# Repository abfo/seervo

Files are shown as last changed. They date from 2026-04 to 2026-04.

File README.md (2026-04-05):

# Seervo

An LLM powered ESP32 robot. This is an experiment in embodied AI, with a vision model connected to a camera and distance detector and deciding what to do next. For more information check out this [video](https://youtu.be/qIrNDQmVw1A) of the robot in action, and my [blog post](https://ithoughthecamewithyou.com/post/seervo-an-llm-powered-robot) about this project.

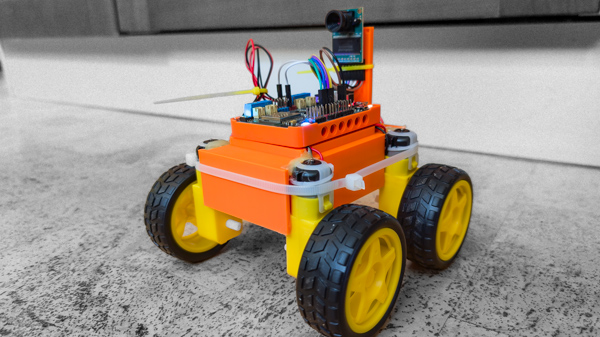
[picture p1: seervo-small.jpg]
Seervo


## Architecture 

For this project I wanted a server to make it easy to see what the robot is doing and to iterate on the prompts and control logic. The server folder has a very simple ASP.NET Core web API. The robot posts an image to the API and gets JSON with the next action to take. I run this in VS Code on Windows but it should run anywhere .NET 10 Core is supported. 

The client folder contains [MicroPython](https://micropython.org/) code to run the robot. There are simple drivers for the camera, motors, sonar, and LEDs and a control loop that calls the API and executes the JSON instructions. 

Lastly the chassis folder contains OpenSCAD and STL files to 3D print a basic chassis that holds the battery, controller, motors and camera. There is also a mounting bracket for a HC-SR04 ultrasonic range detector. 

## Getting Started

Follow the [notes](client/notes.md) in the client folder to flash MicroPython to the ESP32 and assemble the components. Use mpremote to copy python files to the board, and a .env file containing your WiFi SSID and password, i.e.:

```
mprempte cp camera.py :camera.py
```

3D print the chassis. This has alignment holes for the motors and I use a glue gun to hold these in place. I use a cable tie to attach the camera to the mast, and another to wrap around the chassis and secure the battery. 

Start the server up and switch on the robot! You'll need an OpenAI API key as an environment variable. 

## Tips and Ideas

My version is supposed to avoid pets and entertain humans. Edit Instructions.md to give the robot a different mission. 

The server currently uses GPT 5.4 with medium reasoning. I find this to be a good balance of speed and intelligence. It does chew up some money if you leave it running though. Drop down to a cheaper model and/or a lower camera resolution if you need this to be cheaper! 

It would be good to have an option for the robot to call ChatGPT directly, removing the server dependency. 

I'm also considering an image embedding model in parallel to the LLM call, so the robot can more easily detect if it's looking at the same scene and might be stuck.

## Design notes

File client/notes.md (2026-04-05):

# Seervo Client

## Getting Started

I'm using this [Maker-ESP32](https://github.com/nulllaborg/maker-esp32/tree/master?tab=readme-ov-file) board and working with micropython from VS Code. 

Create a virtual environment and install esptool and mpremote:

```python
pip install esptool mpremote
```

Grab the firmware ([this seems to work](https://micropython.org/resources/firmware/ESP32_GENERIC-20251209-v1.27.0.bin)) and install (board mounted as COM5 for me, there is a driver listed but hope not to have to install...):

```python
python -m esptool --port COM5 erase_flash
python -m esptool --port COM5 --baud 460800 write_flash 0x1000 ESP32_GENERIC-20251209-v1.27.0.bin
```

Run a quick test script to blink the LEDs:

```python
from machine import Pin
from neopixel import NeoPixel
import time

np = NeoPixel(Pin(16, Pin.OUT), 4)  # 4 onboard RGB LEDs on GPIO16

while True:
    for i in range(4):
        np[i] = (30, 0, 0)   # red
    np.write()
    time.sleep_ms(300)

    for i in range(4):
        np[i] = (0, 0, 0)    # off
    np.write()
    time.sleep_ms(300)
```

```python
mpremote run main.py
```

LEDs should now be blinking. 

## Camera

For this project I got the Arduino Mega256 SPI camera board (B0067). This wires into SPI/I2C and 3.3v power. There isn't a driver for the ESP32, camera.py handles photo capture. 

## Motors

The Maker-ESP32 has four motor drivers. I'm using [these](https://www.amazon.com/dp/B0D8H89XDY?ref_=ppx_hzsearch_conn_dt_b_fed_asin_title_1) generic motors and wheels. 

## Distance

A HC-SR04 ultrasonic range detector is wired to gnd / 5v / trigger (gpio 25) / echo (gpio 26). Echo need a voltage divider - echo pin to 1kΩ resistor and then from there one wire to gpio 26 and one to ground via a 2kΩ resistor.

```
Echo pin ──── 1kΩ ────┬──── GPIO 26
                       │
                      2kΩ
                       │
                      GND
```

## Power

I'm using [this](https://www.amazon.com/dp/B077Y9HNTF?th=1) battery and [these](https://www.amazon.com/dp/B0CPHJMW47) connectors for the charger and to plug into the Maker board. 

## Chassis 

See the Chassis folder for an OpenSCAD design and STL file.

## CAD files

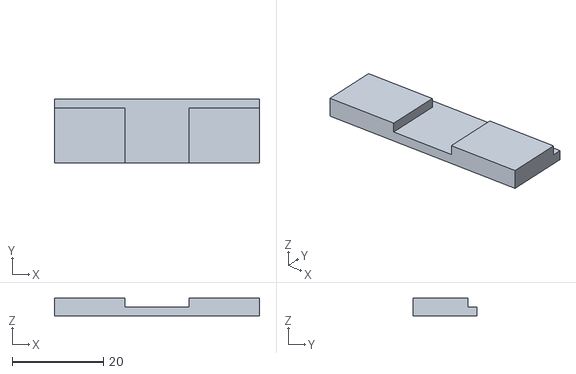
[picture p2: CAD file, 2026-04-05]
chassis/hc-sr04-plate.stl
45.0 x 14.0 x 3.95

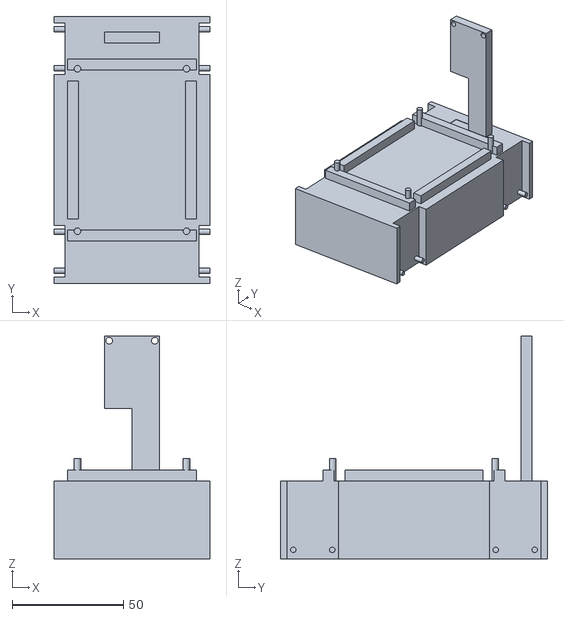
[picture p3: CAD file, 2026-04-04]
chassis/seervo.stl
70.0 x 120.0 x 100.0

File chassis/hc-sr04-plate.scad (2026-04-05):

// HC-SR04 mounting plate

base_w = 45;
base_d = 14;
base_h = 2;

side_w = 15.5;
side_d = 12;
side_h = 1.95;

union() {
    // Base plate
    cube([base_w, base_d, base_h], center = false);

    // Left raised section
    translate([0, 0, base_h])
        cube([side_w, side_d, side_h], center = false);

    // Right raised section
    translate([base_w - side_w, 0, base_h])
        cube([side_w, side_d, side_h], center = false);
}

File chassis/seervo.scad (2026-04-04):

// Outer box dimensions
outer_w = 70;
outer_l = 120;
outer_h = 35;

// Inner battery cavity
inner_w = 53;
inner_h = 32;
front_wall = 3;
back_overlap = 0.2;

// Motor cutouts
motor_cutout_l = 23;
motor_cutout_depth = 5;
corner_offset = 3;
side_overlap = 0.2;

// Motor mounting pegs
motor_peg_d = 2.5;
motor_peg_r = motor_peg_d / 2;
motor_peg_z = 4;         // center 4mm up from bottom
motor_peg_len = 5;       // protrudes 5mm into motor cutout
peg_offset_in_cutout = 2.75;

// Top circuit board mount
board_w = 58;
board_l = 82;
board_wall = 5;
board_wall_h = 5;
side_wire_gap = 10;

// Circuit board standoffs
standoff_inset = 4.5;
standoff_d = 3;
standoff_r = standoff_d / 2;
standoff_h = 10;

// Camera mast
mast_w = 24.5;
mast_l = 5;
mast_h = 65;

// Camera mast holes
mast_hole_d = 3;
mast_hole_r = mast_hole_d / 2;
mast_hole_side_inset = 2;
mast_hole_top_inset = 2;
mast_hole_overlap = 0.2;

// Camera mast cutout
mast_cutout_w = mast_w / 2;
mast_cutout_h = mast_h / 2;
mast_cutout_overlap = 0.2;

front_cutout_y = corner_offset;
rear_cutout_y  = outer_l - corner_offset - motor_cutout_l;

// Board footprint position
board_x0 = (outer_w - board_w) / 2;
board_y0 = (outer_l - board_l) / 2;

// Camera mast position
mast_x0 = (outer_w - mast_w) / 2;
mast_y0 = board_y0 + board_l + ((outer_l - (board_y0 + board_l)) - mast_l) / 2;

// Motor peg centers along the length dimension
motor_peg_y_positions = [
    front_cutout_y + peg_offset_in_cutout,
    front_cutout_y + motor_cutout_l - peg_offset_in_cutout,
    rear_cutout_y  + peg_offset_in_cutout,
    rear_cutout_y  + motor_cutout_l - peg_offset_in_cutout
];

// Mast hole positions
mast_hole_x_positions = [
    mast_x0 + mast_hole_side_inset,
    mast_x0 + mast_w - mast_hole_side_inset
];
mast_hole_z = outer_h + mast_h - mast_hole_top_inset;


// Main chassis body with all cutouts applied
module chassis_body() {
    difference() {
        union() {
            // Outer box
            cube([outer_w, outer_l, outer_h], center = false);

            // Top walls for circuit board mount
            translate([board_x0, board_y0, outer_h]) {
                // Front wall
                cube([board_w, board_wall, board_wall_h], center = false);

                // Back wall
                translate([0, board_l - board_wall, 0])
                    cube([board_w, board_wall, board_wall_h], center = false);

                // Left wall with front/back gaps
                translate([0, side_wire_gap, 0])
                    cube([
                        board_wall,
                        board_l - 2 * side_wire_gap,
                        board_wall_h
                    ], center = false);

                // Right wall with front/back gaps
                translate([board_w - board_wall, side_wire_gap, 0])
                    cube([
                        board_wall,
                        board_l - 2 * side_wire_gap,
                        board_wall_h
                    ], center = false);
            }

            // Circuit board standoffs
            for (x_pos = [board_x0 + standoff_inset, board_x0 + board_w - standoff_inset])
            for (y_pos = [board_y0 + standoff_inset, board_y0 + board_l - standoff_inset]) {
                translate([x_pos, y_pos, outer_h])
                    cylinder(h = standoff_h, r = standoff_r, $fn = 48);
            }

            // Camera mounting mast
            translate([mast_x0, mast_y0, outer_h])
                cube([mast_w, mast_l, mast_h], center = false);
        }

        // Inner battery cavity
        translate([
            (outer_w - inner_w) / 2,
            front_wall,
            (outer_h - inner_h) / 2
        ])
        cube([
            inner_w,
            outer_l - front_wall + back_overlap,
            inner_h
        ], center = false);

        // Motor cutouts: left side
        translate([
            -side_overlap,
            front_cutout_y,
            -side_overlap
        ])
        cube([
            motor_cutout_depth + side_overlap,
            motor_cutout_l,
            outer_h + 2 * side_overlap
        ], center = false);

        translate([
            -side_overlap,
            rear_cutout_y,
            -side_overlap
        ])
        cube([
            motor_cutout_depth + side_overlap,
            motor_cutout_l,
            outer_h + 2 * side_overlap
        ], center = false);

        // Motor cutouts: right side
        translate([
            outer_w - motor_cutout_depth,
            front_cutout_y,
            -side_overlap
        ])
        cube([
            motor_cutout_depth + side_overlap,
            motor_cutout_l,
            outer_h + 2 * side_overlap
        ], center = false);

        translate([
            outer_w - motor_cutout_depth,
            rear_cutout_y,
            -side_overlap
        ])
        cube([
            motor_cutout_depth + side_overlap,
            motor_cutout_l,
            outer_h + 2 * side_overlap
        ], center = false);

        // Camera mast holes
        for (x_pos = mast_hole_x_positions) {
            translate([x_pos, mast_y0 - mast_hole_overlap, mast_hole_z])
                rotate([-90, 0, 0])
                    cylinder(
                        h = mast_l + 2 * mast_hole_overlap,
                        r = mast_hole_r,
                        $fn = 48
                    );
        }

        // Camera mast cutout: lower-right quarter when viewed from behind
        translate([
            mast_x0 - mast_cutout_overlap,
            mast_y0 - mast_cutout_overlap,
            outer_h - mast_cutout_overlap
        ])
        cube([
            mast_cutout_w + mast_cutout_overlap,
            mast_l + 2 * mast_cutout_overlap,
            mast_cutout_h + mast_cutout_overlap
        ], center = false);
    }
}


// Motor pegs added AFTER cutouts so they remain visible
module motor_pegs() {
    // Left side pegs: extend from x=5 back out to x=0 into the cutout
    for (y_pos = motor_peg_y_positions) {
        translate([motor_cutout_depth, y_pos, motor_peg_z])
            rotate([0, -90, 0])
                cylinder(h = motor_peg_len, r = motor_peg_r, $fn = 48);
    }

    // Right side pegs: extend from x=65 out to x=70 into the cutout
    for (y_pos = motor_peg_y_positions) {
        translate([outer_w - motor_cutout_depth, y_pos, motor_peg_z])
            rotate([0, 90, 0])
                cylinder(h = motor_peg_len, r = motor_peg_r, $fn = 48);
    }
}


// Final model
union() {
    chassis_body();
    motor_pegs();
}

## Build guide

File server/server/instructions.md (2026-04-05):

# Robot Control

## Overview

You are a robot controller. You will be provided with a view from the robot's forward facing camera and a distance in meters to the closest object directly in front of the robot. You respond with motor and light controls in JSON format described below. Your objective is to explore your environment and visit four different rooms (a dining room, a kitchen, a hall and a living room). You should entertain any people you find with a small dance, and run away from any pets. It is more important to avoid pets than to entertain people. It's OK to visit rooms multiple times.

As your senses only face forwards you should move in that direction when possible and execute a tank turn to rotate in place when searching for a new direction to travel. Is is recommended that you operate your motors at speed 400 (so 400, 400 to move forwards, -400, 400 to turn, etc). Given this speed use the formula t = (1117.3 * d) + 72.2 to calculate how long to run the motors. In this formula t is time in milliseconds and d is distance in meters. For rotation use t = (2.8 * a) + 100. t is time in milliseconds again and a is angle in degrees. 15 degrees is a good amount to rotate when searching for a clear path forward. If you see a pet, rotate 180 degrees and then start searching for a safe escape path. 

Use your memories to store observations about controlling the robot and navigating your environment. If you see that you are behaving repetitively then try something new. You are brave and favor motion over caution. Try to keep moving as far as possible and explore as much as you can. Do not obsess over finding the right route. If you have space to move forwards, then move. Don't keep turning and rejecting what you see, when you can move, move. If you have less than 0.2 meters in front then rotate and search for a clear path. 

## Example JSON

You always respond with a JSON object following the pattern below. Do not escape the JSON, or include an explanation or other extra text. The JSON object is
being sent to the robot by a web service and will break if you don't follow the format carefully. Here is an example of a valid JSON response:

{
  "colors": [
    { "r": 30, "g": 10, "b": 5 },
    { "r": 25, "g": 10, "b": 0 },
    { "r": 15, "g": 15, "b": 30 },
    { "r": 30, "g": 0, "b": 15 }
  ],
  "duration": 0,
  "leftSpeed": 512,
  "rightSpeed": 512,
  "motorDuration": 300,
  "memory": "I see a wall ahead, I should turn left next time."
}

- colors is an array of four RGB objects, one for each LED. Note that these LEDs are very bright, so 30 is a sensible maximum for each color channel 
unless there is an emergency (like trying to startle an animal). 
- duration is the number of seconds to keep the LEDs on for. Always send 0 as the colors are persistent.
- leftSpeed and rightSpeed are the speeds for the left and right motors, from -1023 (full speed backwards) to 1023 (full speed forwards). A value of 0 means stop. You need at least a speed of 333 to get going. 
- motorDuration is the number of milliseconds to run the motors for. Learn what works well in your environment.
- memory is a string that will be stored and included in the prompt for the next response. You can use this to remember anything you like, but it should be relevant to your task of entertaining the people and avoiding the animals. This can be empty if you have nothing to store. 

You should always change your colors, and always move, even if just a little bit.

## Your Memories

The first memory is a summary of everything you have learned so far.

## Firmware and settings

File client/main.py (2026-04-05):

from machine import Pin
import time
import network
import machine
from sonar import Sonar
import urequests
import sys
import gc
from motors import MotorController
from lights import Lights
from camera import ArduCAM

# Valid ranges
COLOR_MIN, COLOR_MAX = 0, 255
DURATION_MIN, DURATION_MAX = 0, 5
SPEED_MIN, SPEED_MAX = -1023, 1023
MOTOR_DURATION_MIN, MOTOR_DURATION_MAX = 0, 5000

def load_env(path='.env'):
    config = {}
    with open(path) as f:
        for line in f:
            line = line.strip()
            if line and not line.startswith('#') and '=' in line:
                key, val = line.split('=', 1)
                config[key.strip()] = val.strip()
    return config

def clamp(val, lo, hi):
    return max(lo, min(hi, val))

env = load_env()
motors = MotorController()
leds = Lights()
sensor = Sonar()

leds.set_all(30, 0, 0)

# connect to WiFi
wlan = network.WLAN()
wlan.active(False)
time.sleep(1)
leds.set_pixel(0, 0, 30, 0)

wlan.active(True)
if not wlan.isconnected():
    print('connecting to network...')
    wlan.connect(env['WIFI_SSID'], env['WIFI_PASS'])
    while not wlan.isconnected():
        machine.idle()

# WiFi connected    
leds.set_pixel(1, 0, 30, 0)

# connect to camera
cam = ArduCAM.create()
leds.set_all(30, 30, 30)

# control loop
while True:
    try:
        gc.collect()
        time.sleep(0.5)
        data = cam.capture()
        distance = round(sensor.distance_m(), 2)
        url = 'http://192.168.50.2:5090/next?distance={}'.format(distance)
        response = urequests.post(url,
                                  data=data,
                                  headers={'Content-Type': 'image/jpeg'})
        del data
        result = response.json()
        response.close()

        colors = [
            {
                'r': clamp(c['r'], COLOR_MIN, COLOR_MAX),
                'g': clamp(c['g'], COLOR_MIN, COLOR_MAX),
                'b': clamp(c['b'], COLOR_MIN, COLOR_MAX),
            }
            for c in result['colors']
        ]
        duration = clamp(result['duration'], DURATION_MIN, DURATION_MAX)
        left_speed = clamp(result['leftSpeed'], SPEED_MIN, SPEED_MAX)
        right_speed = clamp(result['rightSpeed'], SPEED_MIN, SPEED_MAX)
        motor_duration = clamp(result['motorDuration'], MOTOR_DURATION_MIN, MOTOR_DURATION_MAX)

        leds.update(colors)
        time.sleep(duration)

        if motor_duration > 0 and (left_speed != 0 or right_speed != 0):
            motors.drive(left_speed, right_speed, motor_duration)
        
    except Exception as e:
        try:
            sys.print_exception(e)
            leds.set_all(60, 0, 0)
            motors.stop()
            time.sleep(5)
        except:
            pass

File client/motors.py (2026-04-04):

from machine import Pin, PWM
import time


class MotorController:
    """
    Tank-drive controller for Maker-ESP32 with 4 DC motors.
    Left:  M1 (GPIO 27, 13), M3 (GPIO 17, 12)
    Right: M2 (GPIO 4, 2),   M4 (GPIO 14, 15)
    """

    def __init__(self, freq=1000):
        self._m1a = PWM(Pin(27), freq=freq, duty=0)
        self._m1b = PWM(Pin(13), freq=freq, duty=0)
        self._m2a = PWM(Pin(2),  freq=freq, duty=0)
        self._m2b = PWM(Pin(4),  freq=freq, duty=0)
        self._m3a = PWM(Pin(17), freq=freq, duty=0)
        self._m3b = PWM(Pin(12), freq=freq, duty=0)
        self._m4a = PWM(Pin(14), freq=freq, duty=0)
        self._m4b = PWM(Pin(15), freq=freq, duty=0)

    def _set_side(self, motors, speed):
        """Set a pair of motors. Positive = forward, negative = backward."""
        forward = speed >= 0
        duty = min(abs(speed), 1023)
        for ma, mb in motors:
            if forward:
                ma.duty(duty)
                mb.duty(0)
            else:
                ma.duty(0)
                mb.duty(duty)

    def _left_motors(self):
        return [(self._m1a, self._m1b), (self._m3a, self._m3b)]

    def _right_motors(self):
        return [(self._m2a, self._m2b), (self._m4a, self._m4b)]

    def drive(self, left_speed, right_speed, duration_ms):
        """
        Drive motors for duration_ms.
        Speeds range from -1023 (full reverse) to 1023 (full forward).
        """
        self._set_side(self._left_motors(), left_speed)
        self._set_side(self._right_motors(), right_speed)
        time.sleep_ms(duration_ms)
        self.stop()

    def stop(self):
        """Stop all motors."""
        for ma, mb in self._left_motors() + self._right_motors():
            ma.duty(0)
            mb.duty(0)

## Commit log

2026-03-29 Python installed, wifi working, camera working
2026-03-29 Set LEDs from server call
2026-03-29 LLM decides LED colors based on image input.
2026-03-29 Motor control and external instructions.
2026-03-29 First version of chassis
    [seervo.scad, seervo.stl]
2026-03-29 Motor control
2026-04-04 Improve chassis
2026-04-04 Getting started
    [seervo.scad, seervo.stl]
2026-04-05 Mounting plate for ultrasonic detector.
    [hc-sr04-plate.scad, hc-sr04-plate.stl]
2026-04-05 Ultrasonic range finder instructions
